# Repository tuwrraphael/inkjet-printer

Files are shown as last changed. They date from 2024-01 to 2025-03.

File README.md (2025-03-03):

# Inkjet Printer

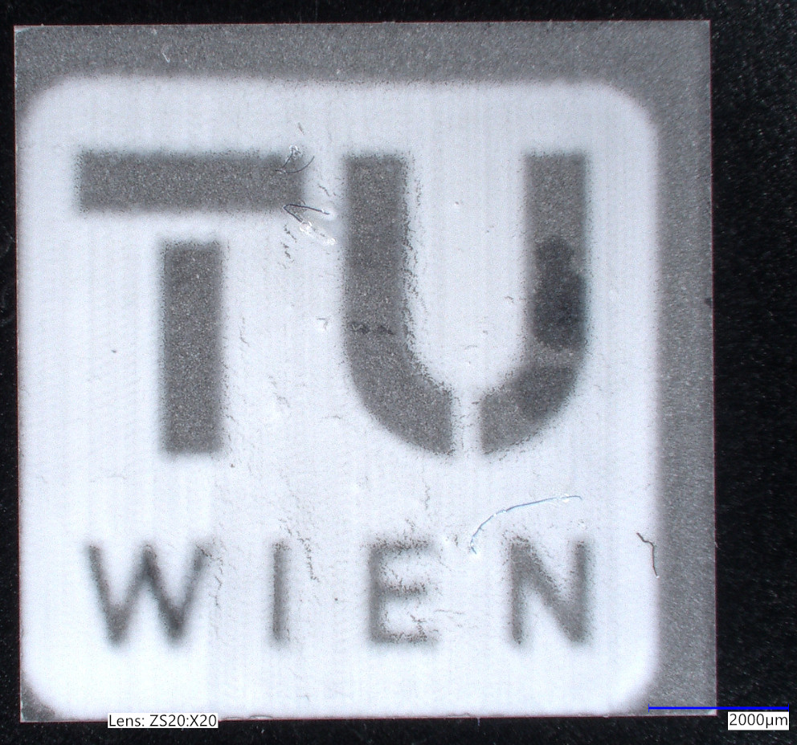
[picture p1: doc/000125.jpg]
A microscope image of a printed TU Wien logo on a 10mm x 10mm substrate.


This repository contains the code, PCB, and CAD of the custom-designed inkjet printer for printing ceramic thin films, which was created as part of the master thesis [Development of an Inkjet Printer for Electrolyte Layers of Oxygen Ion Batteries](https://doi.org/10.34726/hss.2024.116604).
<br clear="right"/>

---

See a preview of the control software: [https://tuwrraphael.github.io/inkjet-printer/](https://tuwrraphael.github.io/inkjet-printer/).

<p align="center">
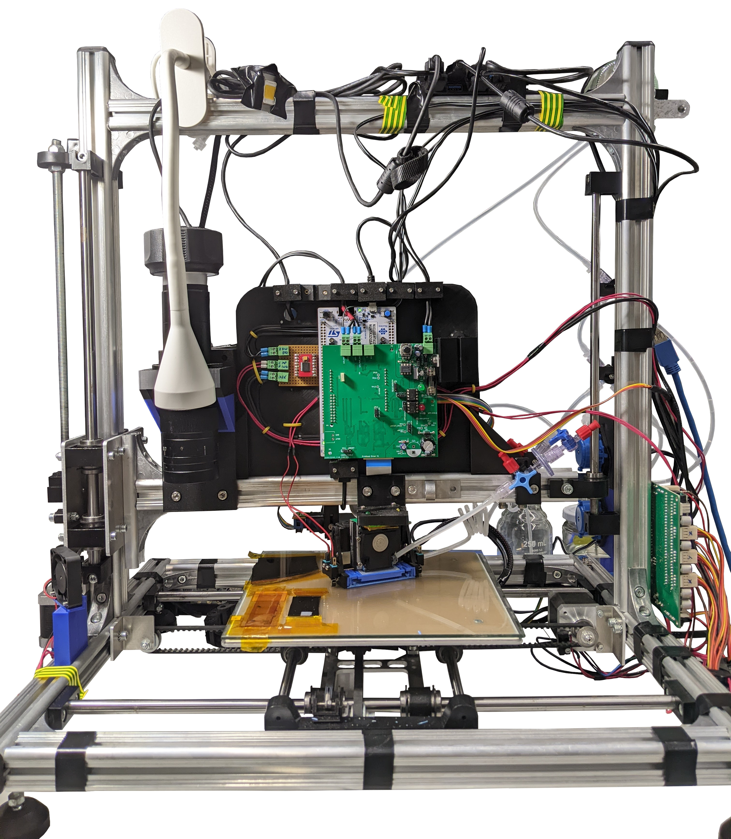
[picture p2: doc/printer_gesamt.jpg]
An overview image of the implemented inkjet printer.
 
 <br>
 An overview image of the implemented inkjet printer.
</p>

Details about the printer, challenges and design decisions, its application and evaluation can be found in the [thesis](https://repositum.tuwien.at/bitstream/20.500.12708/208972/1/Hauk%20Raphael%20-%202024%20-%20Development%20of%20an%20Inkjet%20Printer%20for%20Electrolyte%20Layers%20o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).

Repository structure:
* [inkjet-printer-app](inkjet-printer-app): A web app that controls the printer, is used for planning print jobs, print monitoring & evaluation, calibration and maintenance. Runs in a browser using WebUSB and WebSerial for communicating with the hardware. A deployed version to test an be found [here](https://tuwrraphael.github.io/inkjet-printer/).
* [inkjet-printer-zephyr](inkjet-printer-zephyr): The Zephyr based firmware of the printhead drive electronics.
* [pcbs/Xaar128-Driver](pcbs/Xaar128-Driver): The main PBC design of the printhead drive electronics.
* [cad](cad): Various CAD files of attachments added to the printer.

## Cite this work
The main purpose of publishing this repository is to provide insights into the development of a custom inkjet printer. If you got inspired or found parts of this project useful, please cite the thesis.
~~~
@mastersthesis{HaukRaphael2024DoaI,
  title = {Development of an Inkjet Printer for Electrolyte Layers of Oxygen Ion Batteries},
  author = {Hauk, Raphael},
  year    = 2024,
  school  = {TU Wien},
  address = {Vienna, Austria},
  type    = {{Master's thesis}},
  note     = {Available at: \url{https://doi.org/10.34726/hss.2024.116604}}
}
~~~

## Acknowledgements
This research was funded in part by the Austrian Science Fund (FWF) [10.55776/COE5](https://doi.org/10.55776/COE5).

## Licensing
The firmware builds on Zephyr Project, which is licensed under the Apache License 2.0.
Tools and libraries used in the control software are listed in the app [here](https://tuwrraphael.github.io/inkjet-printer/info).

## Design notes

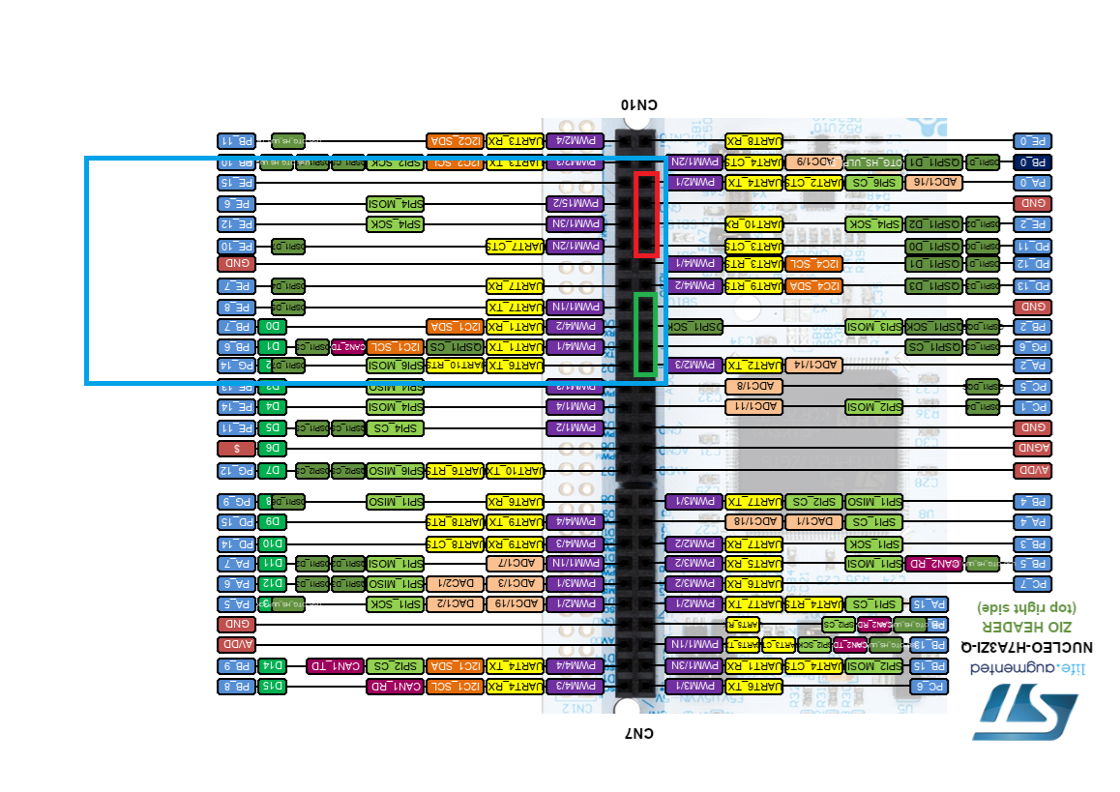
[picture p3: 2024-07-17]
pcbs/pump/pump-pins.png

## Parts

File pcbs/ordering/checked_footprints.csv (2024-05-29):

Value | Footprint | RSBestNr
10u >72V E | Capacitor_THT:CP_Radial_D5.0mm_P2.00mm | 228-7079
220u >72V E | Capacitor_THT:CP_Radial_D13.0mm_P5.00mm | 711-1734
1u >72V Cer | Capacitor_SMD:C_0805_2012Metric_Pad1.18x1.45mm_HandSolder | 788-3054
2.2u >72V E | Capacitor_THT:CP_Radial_D5.0mm_P2.00mm | 365-4442
100n >16V Film | Capacitor_THT:C_Rect_L7.0mm_W3.5mm_P5.00mm | 463-1765
BZX84C10LT1G 10V | Package_TO_SOT_SMD:SOT-23 | 625-5256
3.3V | Diode_SMD:D_SOD-123F | 792-0936
BZX84C27LT1G 27V | Package_TO_SOT_SMD:SOT-23 | 687-8187
Heatsink | Xaar-Driver:SK68-375-SA | 189-8498
Screw_Terminal_01x02 | RS_PRO:897-1051 | 897-1051 + 897-0998
SolderJumper_2_Bridged | Resistor_SMD:R_0603_1608Metric_Pad0.98x0.95mm_HandSolder | 820-6736
DMN2075U | Package_TO_SOT_SMD:SOT-23 | 751-4143
DMG2305UX | Package_TO_SOT_SMD:SOT-23 | 827-0452
1.2k | Resistor_SMD:R_0603_1608Metric_Pad0.98x0.95mm_HandSolder | 198-5480
31.6k | Resistor_SMD:R_0603_1608Metric_Pad0.98x0.95mm_HandSolder | 708-8877
5.1k | Resistor_SMD:R_0603_1608Metric_Pad0.98x0.95mm_HandSolder | 198-5552
68k | Resistor_SMD:R_0603_1608Metric_Pad0.98x0.95mm_HandSolder | 566-367
1.6k | Resistor_SMD:R_0603_1608Metric_Pad0.98x0.95mm_HandSolder | 242-4070
1k | Resistor_SMD:R_0603_1608Metric_Pad0.98x0.95mm_HandSolder | 678-9875
5.1k >300mW | Resistor_SMD:R_0805_2012Metric_Pad1.20x1.40mm_HandSolder | 721-7804
2k > 700mW | Resistor_SMD:R_2010_5025Metric_Pad1.40x2.65mm_HandSolder | 186-6957
100k | Resistor_SMD:R_0603_1608Metric_Pad0.98x0.95mm_HandSolder | 678-9673
12k > 200mW | Resistor_SMD:R_1206_3216Metric_Pad1.30x1.75mm_HandSolder | 812-1795
200 | Resistor_THT:R_Axial_DIN0207_L6.3mm_D2.5mm_P7.62mm_Horizontal | 148-332
4.7k | Resistor_SMD:R_0603_1608Metric_Pad0.98x0.95mm_HandSolder | 901-3581
2.2k > 600mW | Resistor_SMD:R_2512_6332Metric_Pad1.40x3.35mm_HandSolder | 755-1287
680 | Resistor_SMD:R_0603_1608Metric_Pad0.98x0.95mm_HandSolder | 679-0627
6N135 | Package_DIP:DIP-8_W7.62mm | 691-2316
74HC173 | Package_SO:SO-16_3.9x9.9mm_P1.27mm | 483-6443
NUCLEO-H743ZI2 | Xaar-Driver:NUCLEO-H743 | 193-9787
74AHCT125 | Package_SO:SOIC-14_3.9x8.7mm_P1.27mm | 798-8941
LM317_TO-220 | Package_TO_SOT_THT:TO-220-3_Vertical | 661-6121
LTV-356T | Package_SO:SO-4_4.4x3.6mm_P2.54mm | 691-2079
5.1k | Resistor_SMD:R_0805_2012Metric_Pad1.20x1.40mm_HandSolder | 721-7804
Conn_02x15_Odd_Even | CONN_9-176140-0:CONN_9-176140-0_TYC | 7025214
0 | Resistor_SMD:R_0603_1608Metric_Pad0.98x0.95mm_HandSolder | 820-6736
470 | Resistor_SMD:R_0603_1608Metric_Pad0.98x0.95mm_HandSolder | 566-547
NUCLEO-H743ZI2 | Xaar-Driver:NUCLEO-H743 | 198-8645
10u > 16V Tantal | Capacitor_Tantalum_SMD:CP_EIA-3528-21_Kemet-B_Pad1.50x2.35mm_HandSolder | 136-0203
12k | Resistor_SMD:R_1206_3216Metric_Pad1.30x1.75mm_HandSolder | 812-1795
MCP4725xxx-xCH | Package_TO_SOT_SMD:SOT-23-6_Handsoldering | 669-6290
L7824 | Package_TO_SOT_THT:TO-220-3_Vertical | 298-8564
MC78L05_SOT89 | Xaar-Driver:SOT-89-3 | 714-0679
MCP3021 | Package_TO_SOT_SMD:SOT-23-5_HandSoldering | 738-6011
ISO1541 | Package_SO:SOIC-8_3.9x4.9mm_P1.27mm | 825-3075

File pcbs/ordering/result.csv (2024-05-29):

# | Reference | Qty | Value | Footprint | DNP | Supplier | RSBestNr | Extension | done
1 | C1, C2, C3, C4, C5, C6, C28, C30, C33 | 9 | 100n >16V Cer | Capacitor_SMD:C_0603_1608Metric_Pad1.08x0.95mm_HandSolder | DNP | Elektroplatz |  |  | true
2 | C7, C8, C9, C10, C29, C31 | 6 | 100n >16V Cer | Capacitor_SMD:C_0603_1608Metric_Pad1.08x0.95mm_HandSolder |  | Elektroplatz |  |  | true
3 | C11, C16 | 2 | 1u >72V Cer | Capacitor_SMD:C_0805_2012Metric_Pad1.18x1.45mm_HandSolder | DNP | RS | 788-3054 |  | true
4 | C12, C18 | 2 | 10u >72V E | Capacitor_THT:CP_Radial_D5.0mm_P2.00mm |  | RS | 228-7079 |  | true
5 | C13 | 1 | 220u >72V E | Capacitor_THT:CP_Radial_D13.0mm_P5.00mm |  | RS | 711-1734 |  | true
6 | C14 | 1 | 220u >72V E | Capacitor_THT:CP_Radial_D13.0mm_P5.00mm | DNP | RS | 711-1734 |  | true
7 | C15 | 1 | 1u >72V Cer | Capacitor_SMD:C_0805_2012Metric_Pad1.18x1.45mm_HandSolder |  | RS | 788-3054 |  | true
8 | C17, C19 | 2 | 2.2u >72V E | Capacitor_THT:CP_Radial_D5.0mm_P2.00mm |  | RS | 365-4442 |  | true
9 | C20, C25 | 2 | 10u > 16V Tantal | Capacitor_Tantalum_SMD:CP_EIA-3528-21_Kemet-B_Pad1.50x2.35mm_HandSolder | DNP | RS | 136-0203 | Regulator | true
10 | C21, C22, C23, C24, C26 | 5 | 100n >16V Cer | Capacitor_SMD:C_0603_1608Metric_Pad1.08x0.95mm_HandSolder | DNP | Elektroplatz |  | Regulator | true
11 | C27 | 1 | 100n >16V Film | Capacitor_THT:C_Rect_L7.0mm_W3.5mm_P5.00mm |  | RS | 463-1765 |  | true
12 | D1 | 1 | BZX84C10LT1G 10V | Package_TO_SOT_SMD:SOT-23 |  | RS | 625-5256 |  | true
13 | D3 | 1 | LED green Vf=1.8V | Custom_LED_THT:LED_D5.0mm |  | Elektroplatz |  |  | true
14 | D4 | 1 | LED red Vf=1.6V | Custom_LED_THT:LED_D5.0mm |  | Elektroplatz |  |  | true
15 | D5 | 1 | 3.3V | Diode_SMD:D_SOD-123F |  | RS | 792-0936 |  | true
16 | D6 | 1 | BZX84C27LT1G 27V | Package_TO_SOT_SMD:SOT-23 |  | RS | 687-8187 |  | true
17 | D7, D10 | 2 | 1N4007 | Diode_THT:D_DO-41_SOD81_P10.16mm_Horizontal |  | Elektroplatz |  |  | true
18 | D8 | 1 | 1N4007 | Diode_THT:D_DO-41_SOD81_P12.70mm_Horizontal |  | Elektroplatz |  |  | true
19 | D9 | 1 | 5.1V | Diode_THT:D_DO-35_SOD27_P7.62mm_Horizontal |  | Elektroplatz |  |  | true
20 | F1 | 1 | 630mA/F | FUSE_646_1_LTF:FUSE_646_1_LTF |  | Printerbox |  |  | true
21 | H1, H2, H3, H4 | 4 | MountingHole | MountingHole:MountingHole_2.7mm_M2.5_DIN965 |  | None |  |  | true
22 | HS1 | 1 | Heatsink | Xaar-Driver:SK68-375-SA |  | RS | 189-8498 |  | true
23 | J1, J2, J3, J4, J7 | 5 | Screw_Terminal_01x02 | RS_PRO:897-1051 |  | RS | 897-1051 + 897-0998 |  | true
24 | J5 | 1 | Conn_01x21 | Molex_200528:Molex_200528-0210_1x21-1MP_P1.00mm_Horizontal |  | Printerbox |  |  | true
25 | J6 | 1 | Conn_02x08_Odd_Even | Connector_IDC:IDC-Header_2x08_P2.54mm_Vertical | DNP | RS | 771-8357 |  | true
26 | JP1, JP2, JP4, JP5, JP6, JP7, JP14 | 7 | Jumper_3_Bridged12 | Connector_PinHeader_2.54mm:PinHeader_1x03_P2.54mm_Vertical |  | Elektroplatz |  |  | true
27 | JP3, JP8, JP9, JP13, JP15 | 5 | SolderJumper_2_Bridged | Resistor_SMD:R_0603_1608Metric_Pad0.98x0.95mm_HandSolder |  | RS | 820-6736 |  | true
28 | JP10, JP11, JP12, JP16, JP17, JP18, JP19, JP20 | 8 | SolderJumper_2_Open | Resistor_SMD:R_0603_1608Metric_Pad0.98x0.95mm_HandSolder |  | None |  |  | true
29 | Q1, Q2, Q3, Q4, Q5, Q6, Q9, Q10 | 8 | DMN2075U | Package_TO_SOT_SMD:SOT-23 |  | RS | 751-4143 |  | true
30 | Q7, Q8 | 2 | DMG2305UX | Package_TO_SOT_SMD:SOT-23 |  | RS | 827-0452 |  | true
31 | Q11 | 1 | DMG2305UX | Package_TO_SOT_SMD:SOT-23 | DNP | RS | 827-0452 |  | true
32 | R1 | 1 | 1.2k | Resistor_SMD:R_0603_1608Metric_Pad0.98x0.95mm_HandSolder |  | RS | 198-5480 |  | true
33 | R2 | 1 | 31.6k | Resistor_SMD:R_0603_1608Metric_Pad0.98x0.95mm_HandSolder |  | RS | 708-8877 |  | true
34 | R3, R28 | 2 | 5.1k | Resistor_SMD:R_0805_2012Metric_Pad1.20x1.40mm_HandSolder |  | RS | 721-7804 |  | true
35 | R4 | 1 | 68k | Resistor_SMD:R_0603_1608Metric_Pad0.98x0.95mm_HandSolder |  | RS | 566-367 |  | true
36 | R5, R6 | 2 | 1.6k | Resistor_SMD:R_0603_1608Metric_Pad0.98x0.95mm_HandSolder |  | RS | 242-4070 |  | true
37 | R7, R8, R12, R22, R25, R29, R55, R58 | 8 | 1k | Resistor_SMD:R_0603_1608Metric_Pad0.98x0.95mm_HandSolder |  | RS | 678-9875 |  | true
38 | R9 | 1 | 5.1k >300mW | Resistor_SMD:R_0805_2012Metric_Pad1.20x1.40mm_HandSolder |  | RS | 721-7804 |  | true
39 | R10 | 1 | 2k > 700mW | Resistor_SMD:R_2010_5025Metric_Pad1.40x2.65mm_HandSolder |  | RS | 186-6957 |  | true
40 | R11, R20, R23, R46, R56 | 5 | 100k | Resistor_SMD:R_0603_1608Metric_Pad0.98x0.95mm_HandSolder |  | RS | 678-9673 |  | true
41 | R13 | 1 | 20k | Resistor_SMD:R_0603_1608Metric_Pad0.98x0.95mm_HandSolder |  | Elektroplatz |  |  | true
42 | R14, R15, R16, R17, R21, R26, R43, R44, R45, R50, R51, R52, R54 | 13 | 10k | Resistor_SMD:R_0603_1608Metric_Pad0.98x0.95mm_HandSolder |  | Elektroplatz |  |  | true
43 | R18, R33, R47, R48, R49, R53 | 6 | 10k | Resistor_SMD:R_0603_1608Metric_Pad0.98x0.95mm_HandSolder | DNP | Elektroplatz |  |  | true
44 | R19, R24 | 2 | 100k | Resistor_SMD:R_0603_1608Metric_Pad0.98x0.95mm_HandSolder | DNP | RS | 678-9673 |  | true
45 | R27 | 1 | 12k > 200mW | Resistor_SMD:R_1206_3216Metric_Pad1.30x1.75mm_HandSolder |  | RS | 812-1795 |  | true
46 | R30 | 1 | 200 | Resistor_THT:R_Axial_DIN0207_L6.3mm_D2.5mm_P7.62mm_Horizontal |  | RS | 148-332 |  | true
47 | R31 | 1 | 4.7k | Resistor_SMD:R_0603_1608Metric_Pad0.98x0.95mm_HandSolder |  | RS | 901-3581 |  | true
48 | R32 | 1 | 2.2k > 600mW | Resistor_SMD:R_2512_6332Metric_Pad1.40x3.35mm_HandSolder |  | RS | 755-1287 |  | true
49 | R34, R35, R36 | 3 | 10k | Resistor_SMD:R_0603_1608Metric_Pad0.98x0.95mm_HandSolder | DNP | Elektroplatz |  | Regulator | true
50 | R37, R41 | 2 | 100k | Resistor_SMD:R_0603_1608Metric_Pad0.98x0.95mm_HandSolder | DNP | RS | 678-9673 | Regulator | true
51 | R38 | 1 | 2.2k | Resistor_SMD:R_0603_1608Metric_Pad0.98x0.95mm_HandSolder | DNP | Elektroplatz |  | Regulator | true
52 | R39, R42 | 2 | 12k | Resistor_SMD:R_1206_3216Metric_Pad1.30x1.75mm_HandSolder | DNP | RS | 812-1795 | Regulator | true
53 | R40 | 1 | 3k | Resistor_THT:R_Axial_DIN0207_L6.3mm_D2.5mm_P7.62mm_Horizontal | DNP | Elektroplatz |  | Regulator | true
54 | R57 | 1 | 2.2k | Resistor_SMD:R_0603_1608Metric_Pad0.98x0.95mm_HandSolder |  | Elektroplatz |  |  | true
55 | R59 | 1 | 680 | Resistor_SMD:R_0603_1608Metric_Pad0.98x0.95mm_HandSolder |  | RS | 679-0627 |  | true
56 | RV1 | 1 | 10k RC103B | Potentiometer_THT:Potentiometer_Alps_RK09L_Single_Vertical |  | Elektroplatz |  |  | true
57 | TP1, TP2, TP3, TP4, TP5, TP6, TP7, TP8, TP9, TP10, TP11, TP12, TP13, TP14, TP15 | 15 | TestPoint | Xaar-Driver:TestPoint_Pad_D1.5mm |  | None |  |  | true
58 | U1, U2 | 2 | 6N135 | Package_DIP:DIP-8_W7.62mm |  | RS | 691-2316 |  | true
59 | U3, U21 | 2 | 74HC173 | Package_SO:SO-16_3.9x9.9mm_P1.27mm |  | RS | 483-6443 |  | true
60 | U4 | 1 | NUCLEO-H743ZI2 | Xaar-Driver:NUCLEO-H743 |  | RS | 198-8645 |  | true
61 | U5, U6, U7, U12 | 4 | TXB0104D | Package_SO:SOIC-14_3.9x8.7mm_P1.27mm | DNP | RS | 709-2778 |  | true
62 | U8, U9, U10, U20 | 4 | 74AHCT125 | Package_SO:SOIC-14_3.9x8.7mm_P1.27mm |  | RS | 798-8941 |  | true
63 | U11 | 1 | LM317_TO-220 | Package_TO_SOT_THT:TO-220-3_Vertical |  | RS | 661-6121 |  | true
64 | U13 | 1 | MCP4725xxx-xCH | Package_TO_SOT_SMD:SOT-23-6_Handsoldering | DNP | RS | 669-6290 | Regulator | true
65 | U14 | 1 | ISO1541 | Package_SO:SOIC-8_3.9x4.9mm_P1.27mm | DNP | RS | 825-3075 | Regulator | true
66 | U15 | 1 | L7824 | Package_TO_SOT_THT:TO-220-3_Vertical | DNP | RS | 298-8564 | Regulator | true
67 | U16 | 1 | MC78L05_SOT89 | Xaar-Driver:SOT-89-3 | DNP | RS | 714-0679 | Regulator | true
68 | U17 | 1 | TLC272 | Package_DIP:DIP-8_W7.62mm | DNP | Elektroplatz |  | Regulator | true
69 | U18 | 1 | MCP3021 | Package_TO_SOT_SMD:SOT-23-5_HandSoldering | DNP | RS | 738-6011 | Regulator | true
70 | U19 | 1 | LTV-356T | Package_SO:SO-4_4.4x3.6mm_P2.54mm |  | RS | 691-2079 |  | true
71 | U22 | 1 | LIS2DH | Package_LGA:LGA-14_2x2mm_P0.35mm_LayoutBorder3x4y | DNP | None |  |  | true
1 | D1 | 1 | LED yellow Vf=1.6V | Custom_LED_THT:LED_D3.0mm |  | Elektroplatz |  |  | true
2 | D2 | 1 | LED green Vf=1.8V | Custom_LED_THT:LED_D3.0mm |  | Elektroplatz |  |  | true
3 | H1, H2 | 2 | MountingHole | MountingHole:MountingHole_2.7mm_M2.5_DIN965 |  | None |  |  | true
4 | J1 | 1 | Conn_01x21 | Molex_200528:Molex_200528-0210_1x21-1MP_P1.00mm_Horizontal |  | Printerbox |  |  | true
5 | J2 | 1 | Conn_02x15_Odd_Even | CONN_9-176140-0:CONN_9-176140-0_TYC |  | Printerbox | 7025214 |  | true
6 | J3 | 1 | Conn_01x12 | Molex_200528:Molex_52207-1260_1x12-1MP_P1.00mm_Horizontal | DNP | RS | 670-6754 |  | true
7 | Q1 | 1 | DMN2075U | Package_TO_SOT_SMD:SOT-23 |  | RS | 751-4143 |  | true
8 | R1 | 1 | 0 | Resistor_SMD:R_0603_1608Metric_Pad0.98x0.95mm_HandSolder |  | RS | 820-6736 |  | true
9 | R2 | 1 | 10K | Resistor_SMD:R_0603_1608Metric_Pad0.98x0.95mm_HandSolder | DNP | Elekroplatz |  |  | true
10 | R3 | 1 | 1k | Resistor_SMD:R_0603_1608Metric_Pad0.98x0.95mm_HandSolder |  | RS | 678-9875 |  | true
11 | R4 | 1 | 470 | Resistor_SMD:R_0603_1608Metric_Pad0.98x0.95mm_HandSolder |  | RS | 566-547 |  | true
12 | R6 | 1 | 5.1k >300mW | Resistor_SMD:R_0805_2012Metric_Pad1.20x1.40mm_HandSolder |  | RS | 721-7804 |  | true

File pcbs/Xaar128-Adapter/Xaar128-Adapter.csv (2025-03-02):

# | Reference | Qty | Value | Footprint | DNP | Supplier | RSBestNr | Extension
1 | D1 | 1 | LED yellow Vf=1.6V | Custom_LED_THT:LED_D3.0mm |  | Elektroplatz
2 | D2 | 1 | LED green Vf=1.8V | Custom_LED_THT:LED_D3.0mm |  | Elektroplatz
3 | H1, H2 | 2 | MountingHole | MountingHole:MountingHole_2.7mm_M2.5_DIN965 |  | None
4 | J1 | 1 | Conn_01x21 | Molex_200528:Molex_200528-0210_1x21-1MP_P1.00mm_Horizontal |  | Printerbox
5 | J2 | 1 | Conn_02x15_Odd_Even | CONN_9-176140-0:CONN_9-176140-0_TYC |  | Printerbox | 7025214
6 | J3 | 1 | Conn_01x12 | Molex_200528:Molex_52207-1260_1x12-1MP_P1.00mm_Horizontal | DNP | RS | 670-6754
7 | Q1 | 1 | DMN2075U | Package_TO_SOT_SMD:SOT-23 |  | RS | 751-4143
8 | R1 | 1 | 0 | Resistor_SMD:R_0603_1608Metric_Pad0.98x0.95mm_HandSolder |  | RS | 820-6736
9 | R2 | 1 | 10K | Resistor_SMD:R_0603_1608Metric_Pad0.98x0.95mm_HandSolder | DNP | Elekroplatz
10 | R3 | 1 | 1k | Resistor_SMD:R_0603_1608Metric_Pad0.98x0.95mm_HandSolder |  | RS | 678-9875
11 | R4 | 1 | 470 | Resistor_SMD:R_0603_1608Metric_Pad0.98x0.95mm_HandSolder |  | RS | 566-547
12 | R6 | 1 | 5.1k >300mW | Resistor_SMD:R_0805_2012Metric_Pad1.20x1.40mm_HandSolder |  | RS | 721-7804

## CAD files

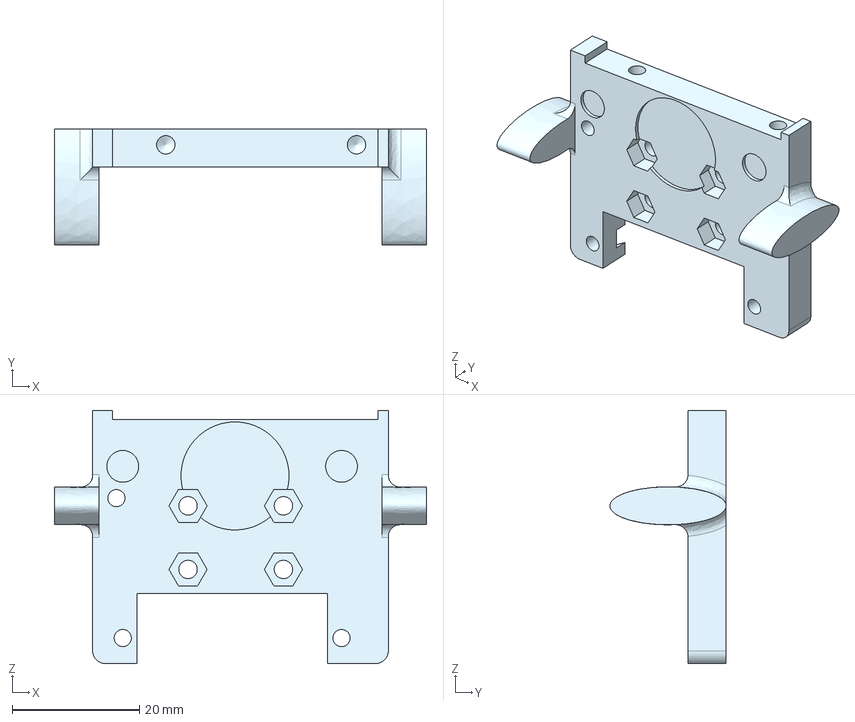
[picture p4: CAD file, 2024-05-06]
cad/Holder - Printheadfixture.step
58.5 x 18.3 x 39.8 mm

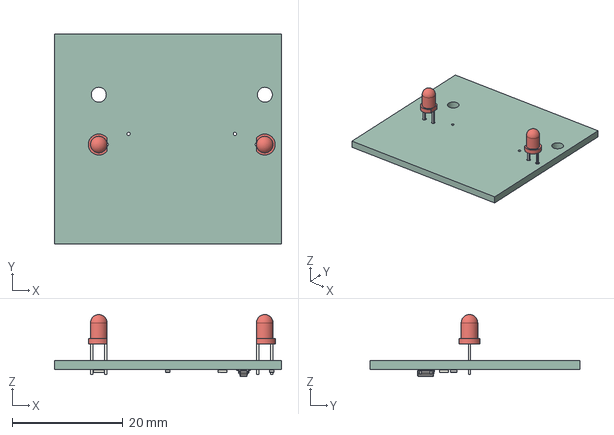
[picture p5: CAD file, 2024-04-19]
cad/Xaar128-Adapter.step
41.0 x 38.0 x 11.2 mm
Xaar128-Adapter PCB

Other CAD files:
cad/Beltspanner.ipt
cad/CameraHolderV2.ipt
cad/Capping_Assembly2.iam
cad/Capping_Insert.ipt
cad/Capping_RotatingArm.ipt
cad/Capping_RotatingCover.ipt
cad/Capping_RotationAnchor.ipt
cad/Capping_RotationGuide.ipt
cad/Capping_RotationGuide_MIR.ipt
cad/Capping_RubberInsert.ipt
cad/Clip.ipt
cad/Dreiwegehahn_Halter.ipt
cad/Dreiwegehahn_Montage45.ipt
cad/Encoder1.iam
cad/Encoder_Mount1.iam
cad/Encoder_Mount1_Slider.ipt
cad/Encoder_Mount2.iam
cad/Encoder_Mount2.ipt
cad/Encoder_Mount3.iam
cad/Encoder_Mount3_Base.ipt
cad/Encoder_Mount3_Washer.ipt
cad/Encoder_Mount3_Wheel.ipt
cad/Enoder_Mount1.ipt
cad/Microscope_Mount.ipt
cad/PCB_Mount_Triangle.ipt
cad/PCB_Plate.ipt
cad/Pressuresensor_Holder.ipt
cad/Pressurevessel_Mount.ipt
cad/Printer_Mount.ipt
cad/Pump_Mount.ipt
cad/Sensor_Montage.ipt
cad/TPiece.ipt
cad/Xaar128.ipt

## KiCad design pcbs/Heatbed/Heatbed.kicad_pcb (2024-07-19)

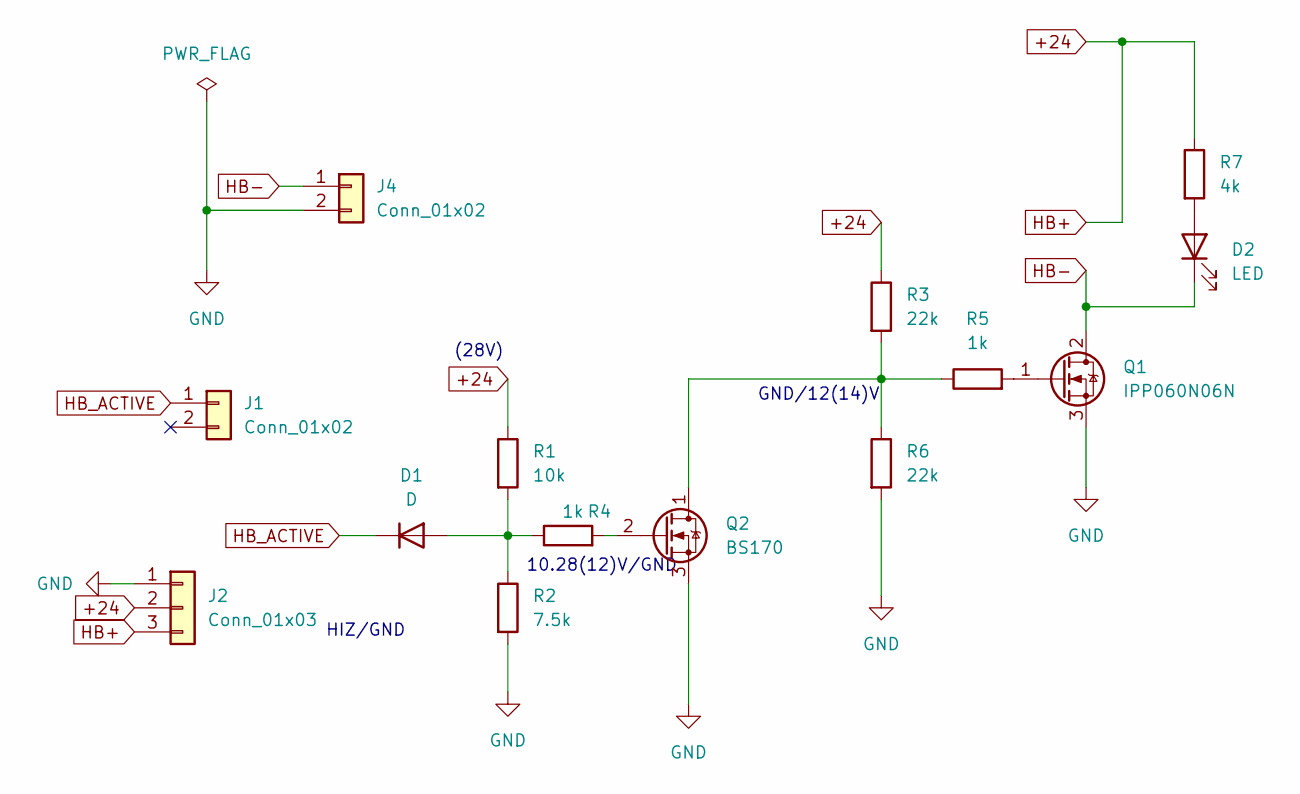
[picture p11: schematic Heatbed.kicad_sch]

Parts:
D1: D; D_A-405_P7.62mm_Horizontal
D2: LED; LED_D3.0mm
J1: Conn_01x02; PinHeader_1x02_P2.54mm_Vertical
J2: Conn_01x03; TerminalBlock_bornier-3_P5.08mm
J4: Conn_01x02; TerminalBlock_bornier-2_P5.08mm
Q1: IPP060N06N; TO-220-3_Vertical
Q2: BS170; TO-92_Inline_Wide
R1: 10k; R_Axial_DIN0204_L3.6mm_D1.6mm_P5.08mm_Horizontal
R2: 7.5k; R_Axial_DIN0204_L3.6mm_D1.6mm_P5.08mm_Horizontal
R3, R6: 22k; R_Axial_DIN0204_L3.6mm_D1.6mm_P5.08mm_Horizontal
R4, R5: 1k; R_Axial_DIN0204_L3.6mm_D1.6mm_P5.08mm_Horizontal
R7: 4k; R_Axial_DIN0204_L3.6mm_D1.6mm_P5.08mm_Horizontal

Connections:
+24: J2.2, J2.3, R1.1, R3.1, R7.1
GND: J2.1, J4.2, Q1.3 (S), Q2.3 (S), R2.2, R6.2
HB-: D2.1 (K), J4.1, Q1.2 (D)
HB_ACTIVE: D1.1 (K), J1.1
unnamed: D1.2 (A), R1.2, R2.1, R4.1
unnamed: D2.2 (A), R7.2
unnamed: Q1.1 (G), R5.2
unnamed: Q2.1 (D), R3.2, R5.1, R6.1
unnamed: Q2.2 (G), R4.2

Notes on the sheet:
HIZ/GND
(28V)
10.28(12)V/GND
GND/12(14)V

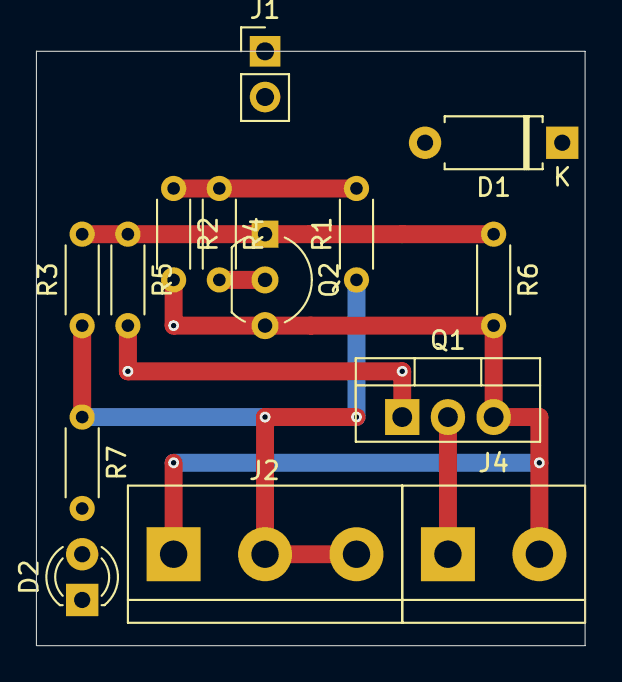
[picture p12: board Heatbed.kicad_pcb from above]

Board: 2 copper layers, 30.5 x 33.0 mm, 14 parts (0 on the bottom side), 9 nets.

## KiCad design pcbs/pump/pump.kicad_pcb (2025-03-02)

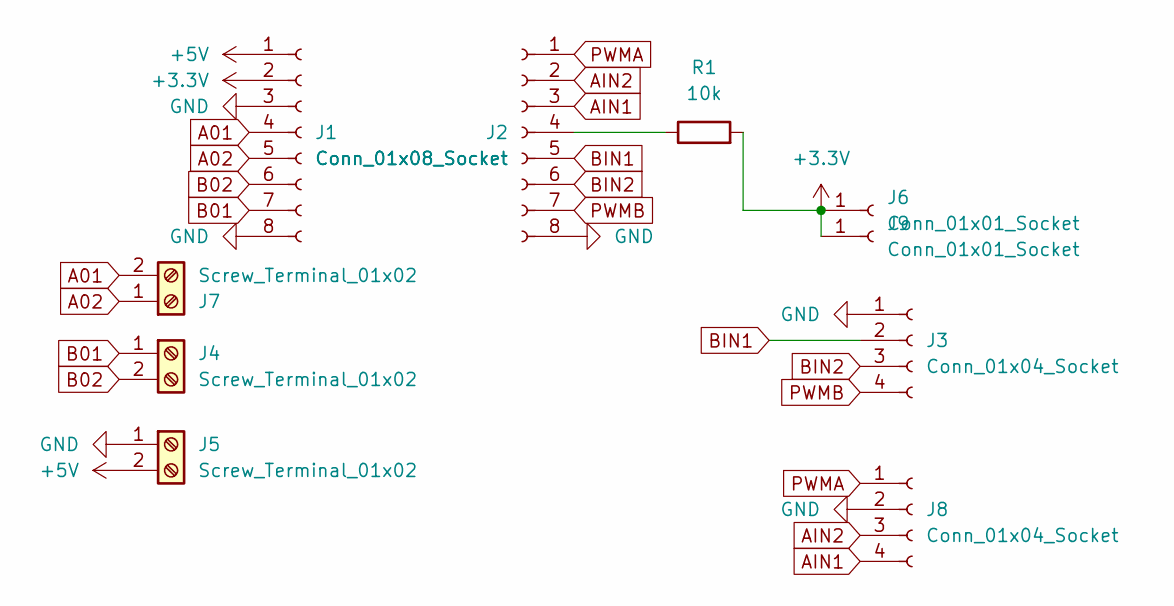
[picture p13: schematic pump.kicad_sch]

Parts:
J1, J2: Conn_01x08_Socket; PinSocket_1x08_P2.54mm_Vertical
J3, J8: Conn_01x04_Socket; PinSocket_1x04_P2.54mm_Vertical
J4, J5, J7: Screw_Terminal_01x02; Steckbarer_Klemmenblock_1x02_5.08mm_horizontal
J6, J9: Conn_01x01_Socket; PinSocket_1x01_P2.54mm_Vertical
R1: 10k; R_Axial_DIN0207_L6.3mm_D2.5mm_P7.62mm_Horizontal

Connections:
+3.3V: J1.2, J6.1, J9.1, R1.2
+5V: J1.1, J5.2
A01: J1.4, J7.2
A02: J1.5, J7.1
AIN1: J2.3, J8.4
AIN2: J2.2, J8.3
B01: J1.7, J4.1
B02: J1.6, J4.2
BIN1: J2.5, J3.2
BIN2: J2.6, J3.3
GND: J1.3, J1.8, J2.8, J3.1, J5.1, J8.2
unnamed: J2.4, R1.1
PWMA: J2.1, J8.1
PWMB: J2.7, J3.4

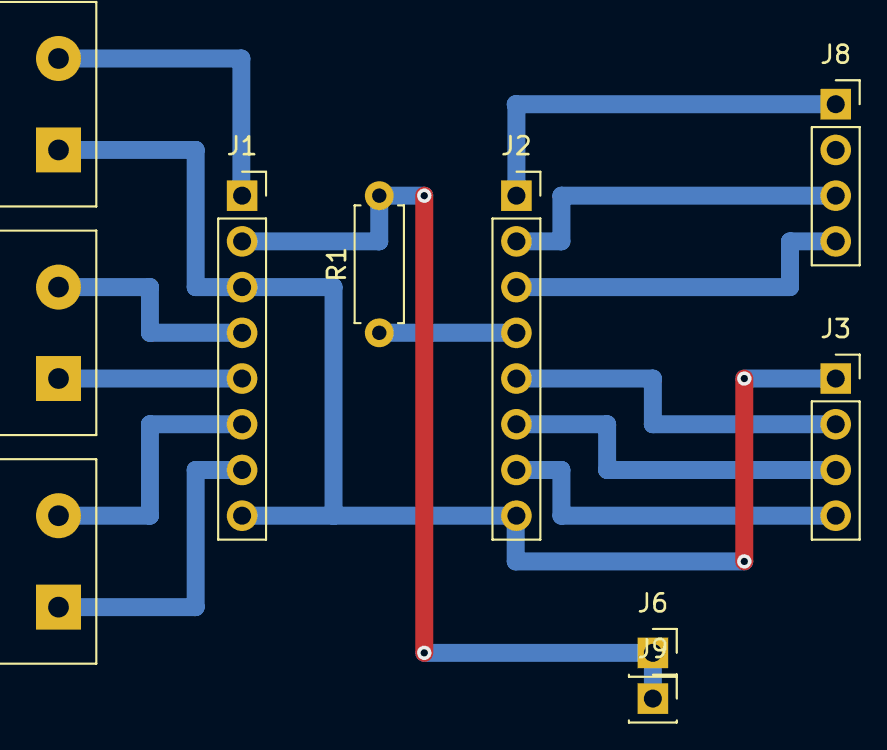
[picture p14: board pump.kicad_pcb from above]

Board: 2 copper layers, 10 parts (0 on the bottom side), 14 nets.

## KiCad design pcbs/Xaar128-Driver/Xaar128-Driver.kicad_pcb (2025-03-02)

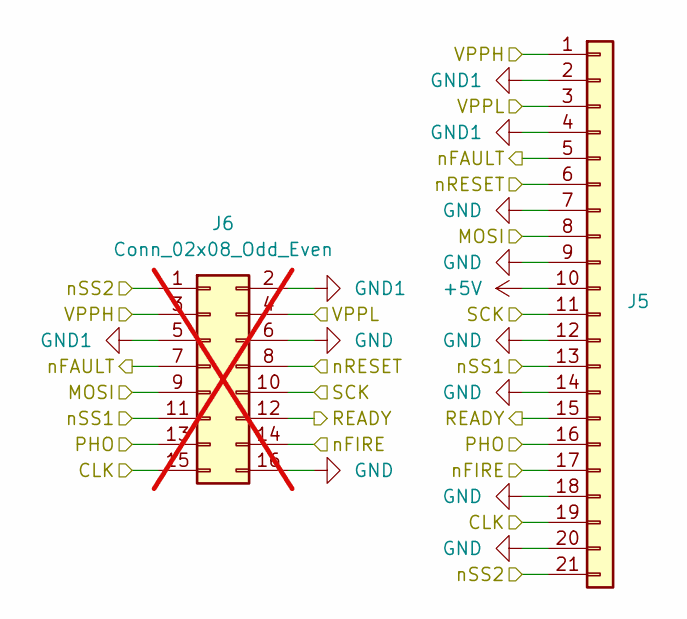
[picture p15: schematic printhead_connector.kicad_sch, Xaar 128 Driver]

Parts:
J5: Conn_01x21; Molex_200528-0210_1x21-1MP_P1.00mm_Horizontal
J6: Conn_02x08_Odd_Even; IDC-Header_2x08_P2.54mm_Vertical; not fitted

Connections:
+5V: J5.10; also elsewhere on the board
/HV Supply/VPPH: J5.1, J6.3; also elsewhere on the board
/HV Supply/VPPL: J5.3, J6.4; also elsewhere on the board
/IO/nFIRE: J5.17, J6.14; also elsewhere on the board
/Level Shift/CLK_OUT: J5.19, J6.15; also elsewhere on the board
/Level Shift/MOSI_OUT: J5.8, J6.9; also elsewhere on the board
/Level Shift/PHO_OUT: J5.16, J6.13; also elsewhere on the board
/Level Shift/READY_IN: J5.15, J6.12; also elsewhere on the board
/Level Shift/SCK_OUT: J5.11, J6.10; also elsewhere on the board
/Level Shift/nFAULT_IN: J5.5, J6.7; also elsewhere on the board
/Level Shift/nRESET_IN: J5.6, J6.8; also elsewhere on the board
/Level Shift/nSS1_OUT: J5.13, J6.11; also elsewhere on the board
/Level Shift/nSS2_OUT: J5.21, J6.1; also elsewhere on the board

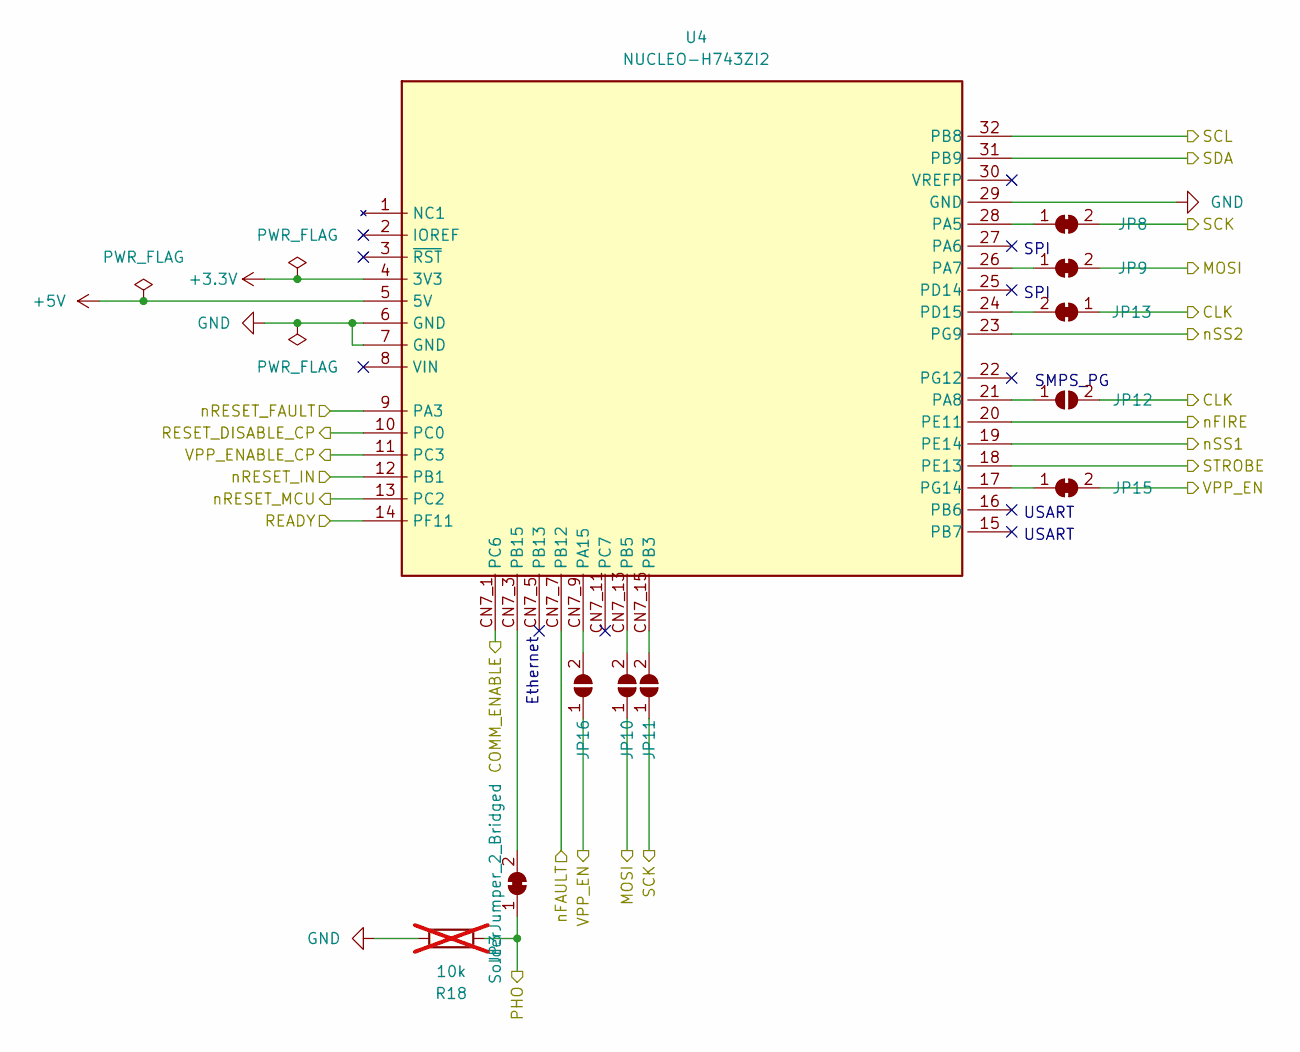
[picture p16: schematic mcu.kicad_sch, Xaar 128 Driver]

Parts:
JP3, JP8, JP9, JP13, JP15: SolderJumper_2_Bridged; R_0603_1608Metric_Pad0.98x0.95mm_HandSolder
JP10, JP11, JP12, JP16: SolderJumper_2_Open; R_0603_1608Metric_Pad0.98x0.95mm_HandSolder
R18: 10k; R_0603_1608Metric_Pad0.98x0.95mm_HandSolder; not fitted
U4: NUCLEO-H743ZI2; NUCLEO-H743

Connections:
+5V: U4.5 (5V); also elsewhere on the board
/ACC/SCL: U4.32 (PB8); also elsewhere on the board
/ACC/SDA: U4.31 (PB9); also elsewhere on the board
/HV Supply/VPP_EN: JP15.2 (B), JP16.1 (A); also elsewhere on the board
/Level Shift/CLK_IN: JP12.2 (B), JP13.1 (A); also elsewhere on the board
/Level Shift/COMM_ENABLE: U4.CN7_1 (PC6); also elsewhere on the board
/Level Shift/MOSI_IN: JP9.2 (B), JP10.1 (A); also elsewhere on the board
/Level Shift/PHO_IN: JP3.1 (A), R18.2; also elsewhere on the board
/Level Shift/READY_OUT: U4.14 (PF11); also elsewhere on the board
/Level Shift/RESET_DISABLE_CP_IN: U4.10 (PC0); also elsewhere on the board
/Level Shift/SCK_IN: JP8.2 (B), JP11.1 (A); also elsewhere on the board
/Level Shift/VPP_EN_CP_IN: U4.11 (PC3); also elsewhere on the board
/Level Shift/nFAULT_OUT: U4.CN7_7 (PB12); also elsewhere on the board
/Level Shift/nFIRE_IN: U4.20 (PE11); also elsewhere on the board
/Level Shift/nRESET_FAULT_OUT: U4.9 (PA3); also elsewhere on the board
/Level Shift/nRESET_OUT: U4.12 (PB1); also elsewhere on the board
/Level Shift/nSS1_IN: U4.19 (PE14); also elsewhere on the board
/Level Shift/nSS2_IN: U4.23 (PG9); also elsewhere on the board
/MCU/STROBE: U4.18 (PE13); also elsewhere on the board
/MCU/nRESET_MCU: U4.13 (PC2); also elsewhere on the board
unnamed: JP3.2 (B), U4.CN7_3 (PB15)
unnamed: JP8.1 (A), U4.28 (PA5)
unnamed: JP9.1 (A), U4.26 (PA7)
unnamed: JP10.2 (B), U4.CN7_13 (PB5)
unnamed: JP11.2 (B), U4.CN7_15 (PB3)
unnamed: JP12.1 (A), U4.21 (PA8)
unnamed: JP13.2 (B), U4.24 (PD15)
unnamed: JP15.1 (A), U4.17 (PG14)
unnamed: JP16.2 (B), U4.CN7_9 (PA15)

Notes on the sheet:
SMPS_PG
SPI
Ethernet
USART

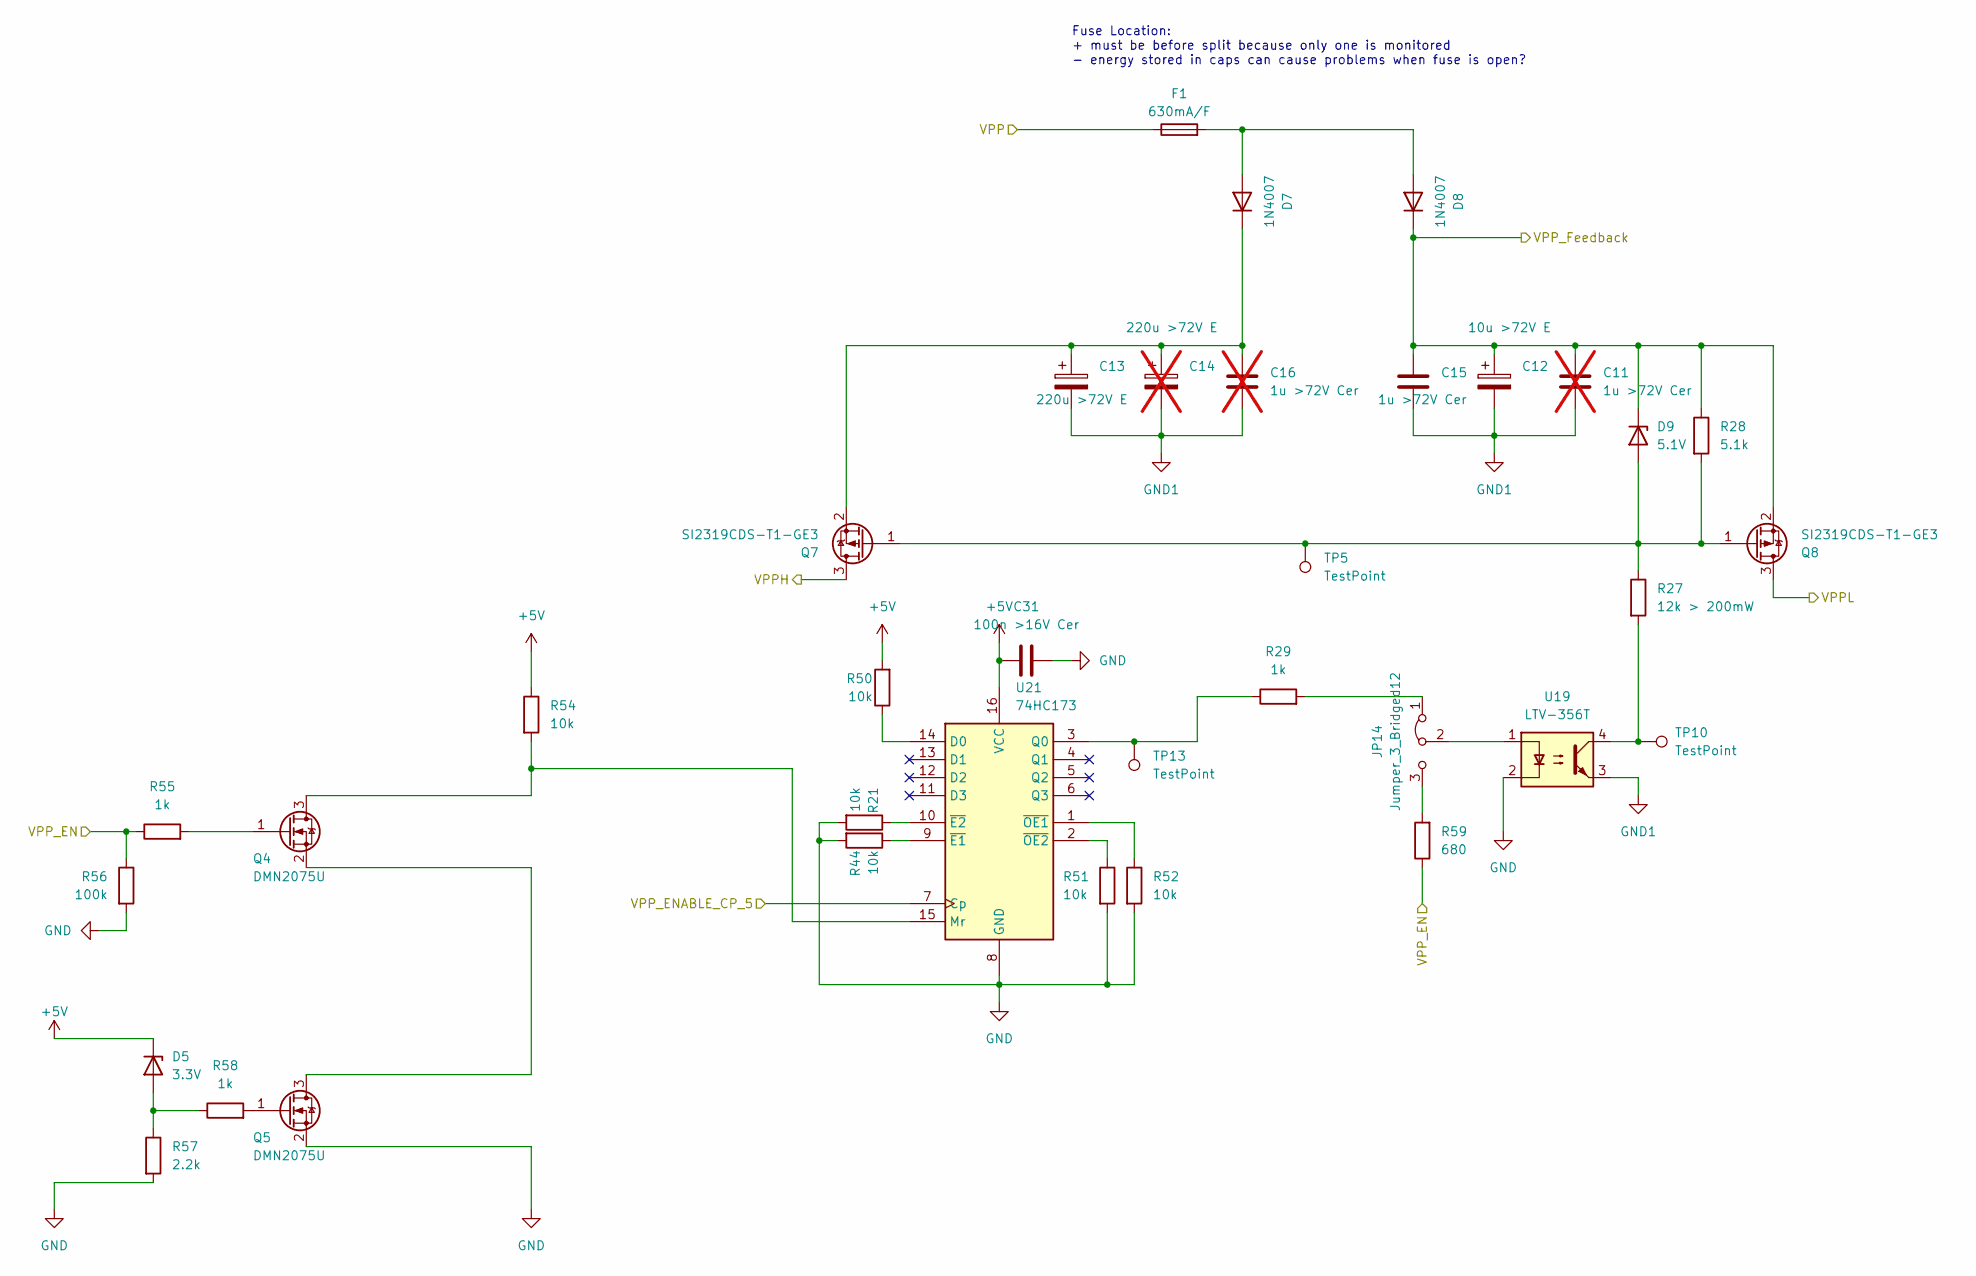
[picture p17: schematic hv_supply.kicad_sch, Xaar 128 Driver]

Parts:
C11, C16: 1u >72V Cer; C_0805_2012Metric_Pad1.18x1.45mm_HandSolder; not fitted
C12: 10u >72V E; CP_Radial_D5.0mm_P2.00mm
C13: 220u >72V E; CP_Radial_D13.0mm_P5.00mm
C14: 220u >72V E; CP_Radial_D13.0mm_P5.00mm; not fitted
C15: 1u >72V Cer; C_0805_2012Metric_Pad1.18x1.45mm_HandSolder
C31: 100n >16V Cer; C_0603_1608Metric_Pad1.08x0.95mm_HandSolder
D5: 3.3V; D_SOD-123F
D7: 1N4007; D_DO-41_SOD81_P10.16mm_Horizontal
D8: 1N4007; D_DO-41_SOD81_P12.70mm_Horizontal
D9: 5.1V; D_DO-35_SOD27_P7.62mm_Horizontal
F1: 630mA/F; FUSE_646_1_LTF
JP14: Jumper_3_Bridged12; PinHeader_1x03_P2.54mm_Vertical
Q4, Q5: DMN2075U; SOT-23
Q7, Q8: SI2319CDS-T1-GE3; SOT-23
R21, R44, R50, R51, R52, R54: 10k; R_0603_1608Metric_Pad0.98x0.95mm_HandSolder
R27: 12k > 200mW; R_1206_3216Metric_Pad1.30x1.75mm_HandSolder
R28: 5.1k; R_0805_2012Metric_Pad1.20x1.40mm_HandSolder
R29, R55, R58: 1k; R_0603_1608Metric_Pad0.98x0.95mm_HandSolder
R56: 100k; R_0603_1608Metric_Pad0.98x0.95mm_HandSolder
R57: 2.2k; R_0603_1608Metric_Pad0.98x0.95mm_HandSolder
R59: 680; R_0603_1608Metric_Pad0.98x0.95mm_HandSolder
TP5, TP10, TP13: TestPoint; TestPoint_Pad_D1.5mm
U19: LTV-356T; SO-4_4.4x3.6mm_P2.54mm
U21: 74HC173; SO-16_3.9x9.9mm_P1.27mm

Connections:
+5V: C31.1, D5.1 (K), R50.2, R54.1, U21.16 (VCC); also elsewhere on the board
/HV Supply/VPP: F1.1; also elsewhere on the board
/HV Supply/VPPH: Q7.3 (D); also elsewhere on the board
/HV Supply/VPPL: Q8.3 (D); also elsewhere on the board
/HV Supply/VPP_EN: R55.1, R56.1, R59.1; also elsewhere on the board
/HV Supply/VPP_ENABLE_CP_5: U21.7 (Cp); also elsewhere on the board
/HV Supply/VPP_Feedback: C11.1, C12.1, C15.1, D8.1 (K), D9.1 (K), Q8.2 (S), R28.1; also elsewhere on the board
unnamed: D5.2 (A), R57.1, R58.1
unnamed: D7.2 (A), D8.2 (A), F1.2
unnamed: C13.1, C14.1, C16.1, D7.1 (K), Q7.2 (S)
unnamed: D9.2 (A), Q7.1 (G), Q8.1 (G), R27.1, R28.2, TP5.1
unnamed: JP14.1 (A), R29.2
unnamed: JP14.3 (B), R59.2
unnamed: JP14.2 (C), U19.1
unnamed: Q4.3 (D), R54.2, U21.15 (Mr)
unnamed: Q4.1 (G), R55.2
unnamed: Q4.2 (S), Q5.3 (D)
unnamed: Q5.1 (G), R58.2
unnamed: R27.2, TP10.1, U19.4
unnamed: R50.1, U21.14 (D0)
unnamed: R29.1, TP13.1, U21.3 (Q0)
unnamed: R44.1, U21.9 (~E1)
unnamed: R21.1, U21.10 (~E2)
unnamed: R52.1, U21.1 (~OE1)
unnamed: R51.1, U21.2 (~OE2)

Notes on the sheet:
Fuse Location: + must be before split because only one is monitored - energy stored in caps can cause problems when fuse is open?

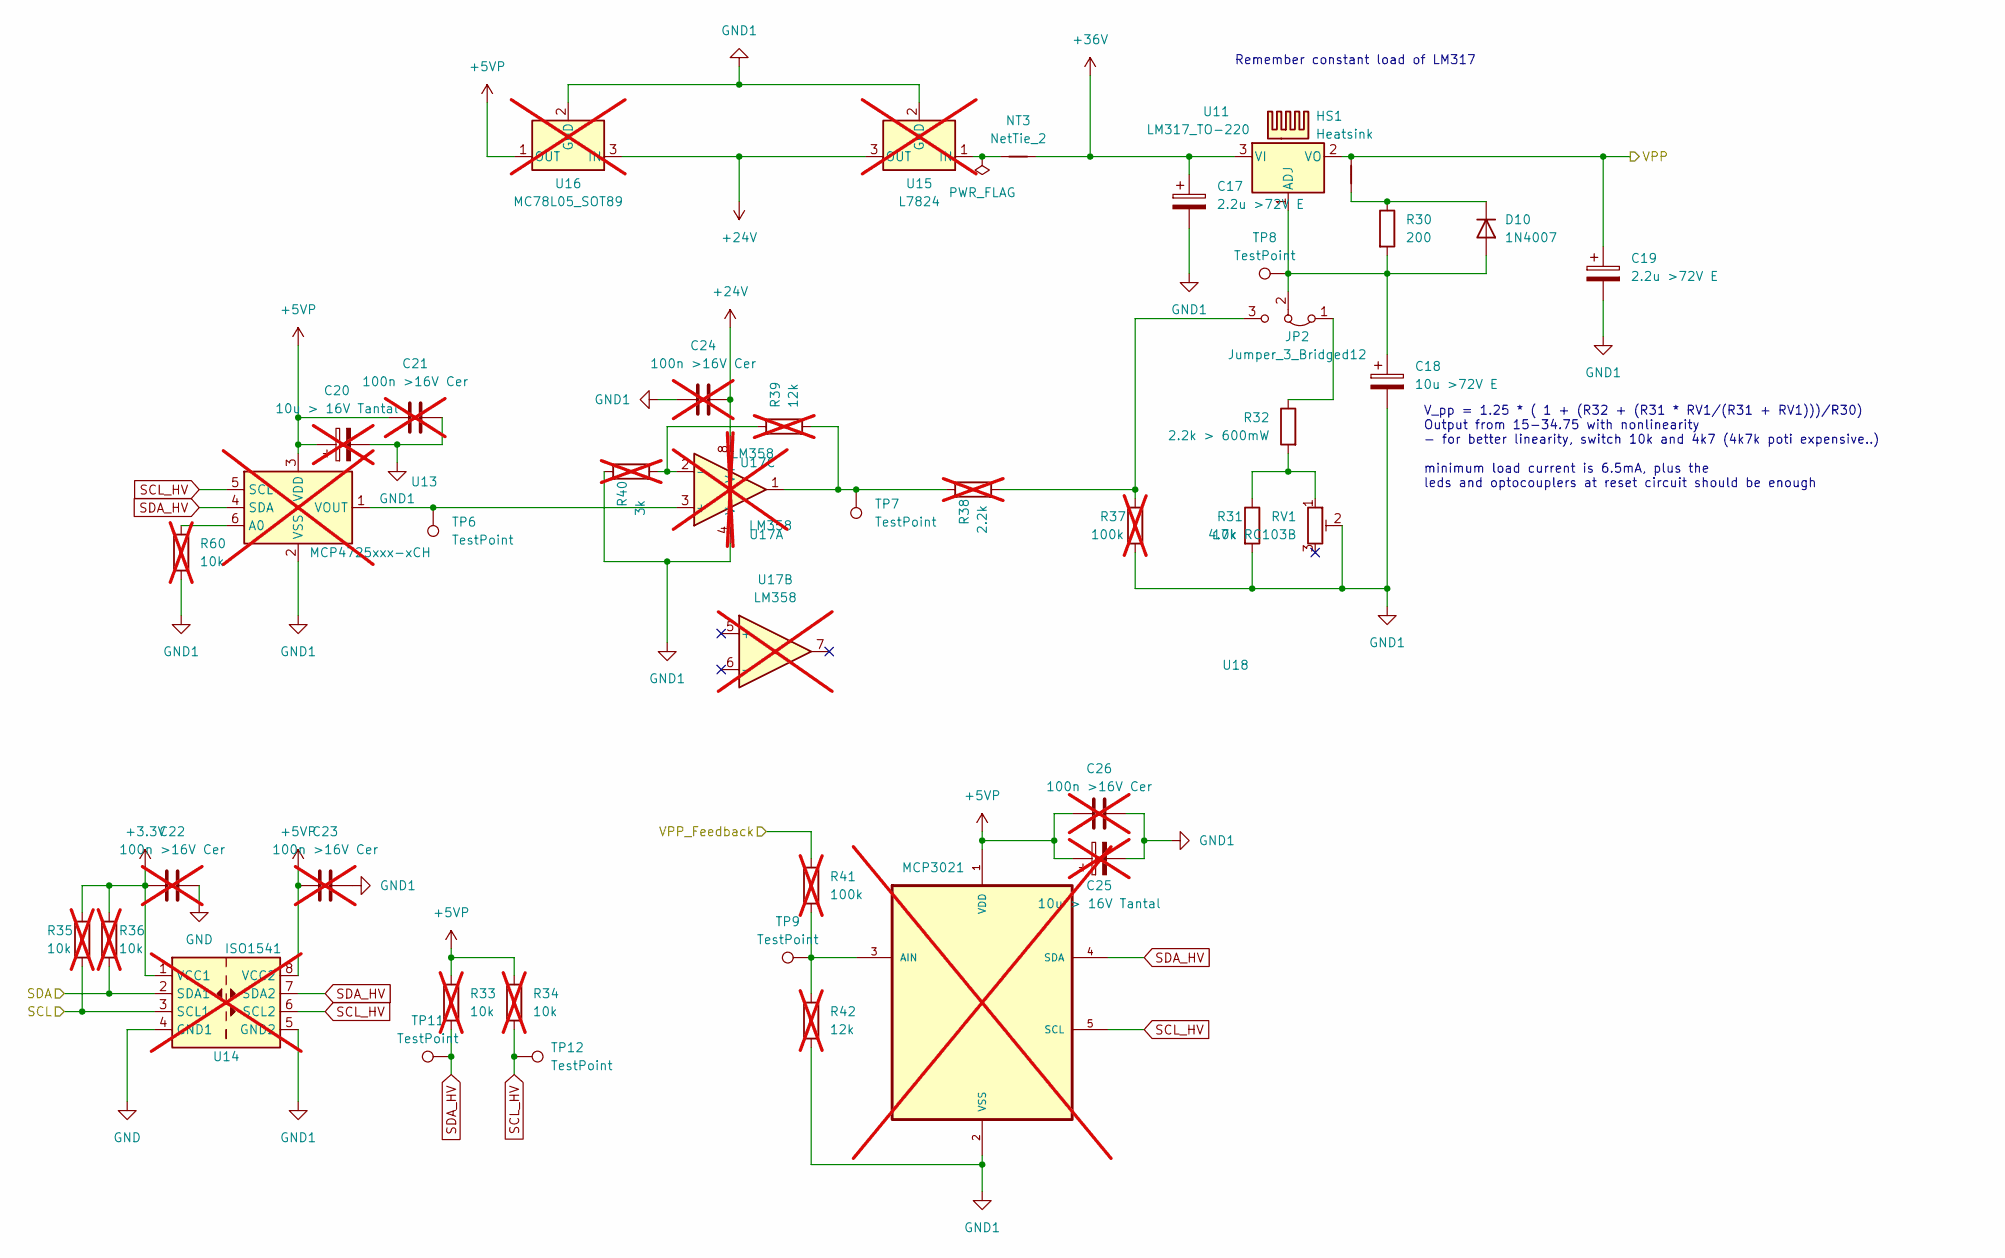
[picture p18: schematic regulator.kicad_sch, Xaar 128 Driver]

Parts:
C17, C19: 2.2u >72V E; CP_Radial_D5.0mm_P2.00mm
C18: 10u >72V E; CP_Radial_D5.0mm_P2.00mm
C20, C25: 10u > 16V Tantal; CP_EIA-3528-21_Kemet-B_Pad1.50x2.35mm_HandSolder; not fitted
C21, C22, C23, C24, C26: 100n >16V Cer; C_0603_1608Metric_Pad1.08x0.95mm_HandSolder; not fitted
D10: 1N4007; D_DO-41_SOD81_P10.16mm_Horizontal
HS1: Heatsink; SK68-375-SA
JP2: Jumper_3_Bridged12; PinHeader_1x03_P2.54mm_Vertical
NT1, NT3: NetTie_2; NetTie-2_SMD_Pad0.5mm
R30: 200; R_Axial_DIN0207_L6.3mm_D2.5mm_P7.62mm_Horizontal
R31: 4.7k; R_0603_1608Metric_Pad0.98x0.95mm_HandSolder
R32: 2.2k > 600mW; R_2512_6332Metric_Pad1.40x3.35mm_HandSolder
R33, R34, R35, R36, R60: 10k; R_0603_1608Metric_Pad0.98x0.95mm_HandSolder; not fitted
R37, R41: 100k; R_0603_1608Metric_Pad0.98x0.95mm_HandSolder; not fitted
R38: 2.2k; R_0603_1608Metric_Pad0.98x0.95mm_HandSolder; not fitted
R39, R42: 12k; R_1206_3216Metric_Pad1.30x1.75mm_HandSolder; not fitted
R40: 3k; R_Axial_DIN0207_L6.3mm_D2.5mm_P7.62mm_Horizontal; not fitted
RV1: 10k RC103B; Potentiometer_Alps_RK09L_Single_Vertical
TP6, TP7, TP8, TP9, TP11, TP12: TestPoint; TestPoint_Pad_D1.5mm
U11: LM317_TO-220; TO-220-3_Vertical
U13: MCP4725xxx-xCH; SOT-23-6_Handsoldering; not fitted
U14: ISO1541; SOIC-8_3.9x4.9mm_P1.27mm; not fitted
U15: L7824; TO-220-3_Vertical; not fitted
U16: MC78L05_SOT89; SOT-89-3; not fitted
U17: LM358; DIP-8_W7.62mm; not fitted
U18: MCP3021; SOT-23-5_HandSoldering; not fitted

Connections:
+5VP: C20.1, C21.1, C23.2, C25.1, C26.1, R33.1, R34.1, U13.3 (VDD), U14.8 (VCC2), U16.1 (OUT), U18.1 (VDD)
+24V: C24.2, U15.3 (OUT), U16.3 (IN), U17.8 (V+)
+36V: C17.1, NT3.2, U11.3 (VI); also elsewhere on the board
/ACC/SCL: R35.2, U14.3 (SCL1); also elsewhere on the board
/ACC/SDA: R36.2, U14.2 (SDA1); also elsewhere on the board
/HV Supply/VPP: C19.1, NT1.1, U11.2 (VO); also elsewhere on the board
/HV Supply/VPP_Feedback: R41.1; also elsewhere on the board
unnamed: C18.1, D10.2 (A), JP2.2 (C), R30.2, TP8.1, U11.1 (ADJ)
unnamed: D10.1 (K), NT1.2, R30.1
unnamed: JP2.1 (A), R32.1
unnamed: JP2.3 (B), R37.1, R38.2
unnamed: R31.1, R32.2, RV1.1
unnamed: R38.1, R39.2, TP7.1, U17.1
unnamed: R60.1, U13.6 (A0)
unnamed: TP6.1, U13.1 (VOUT), U17.3 (+)
unnamed: NT3.1, U15.1 (IN)
unnamed: R39.1, R40.2, U17.2 (-)
unnamed: R41.2, R42.1, TP9.1, U18.3 (AIN)
SCL_HV: R34.2, TP12.1, U13.5 (SCL), U14.6 (SCL2), U18.5 (SCL)
SDA_HV: R33.2, TP11.1, U13.4 (SDA), U14.7 (SDA2), U18.4 (SDA)

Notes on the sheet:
Remember constant load of LM317
V_pp = 1.25 * ( 1 + (R32 + (R31 * RV1/(R31 + RV1)))/R30) Output from 15-34.75 with nonlinearity - for better linearity, switch 10k and 4k7 (4k7k poti expensive..) minimum load current is 6.5mA, plus the leds and optocouplers at reset circuit should be enough

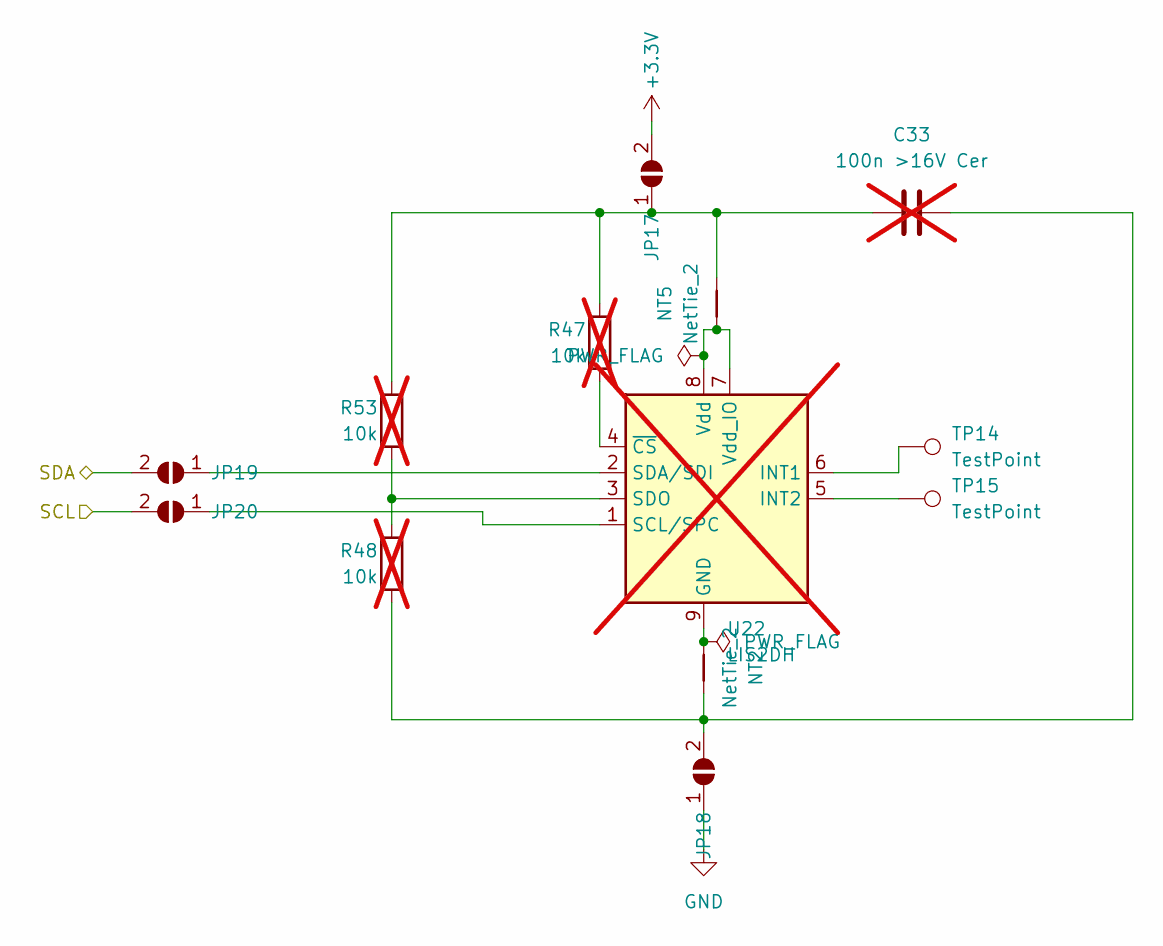
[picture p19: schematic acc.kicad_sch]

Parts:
C33: 100n >16V Cer; C_0603_1608Metric_Pad1.08x0.95mm_HandSolder; not fitted
JP17, JP18, JP19, JP20: SolderJumper_2_Open; R_0603_1608Metric_Pad0.98x0.95mm_HandSolder
NT2, NT5: NetTie_2; NetTie-2_SMD_Pad0.5mm
R47, R48, R53: 10k; R_0603_1608Metric_Pad0.98x0.95mm_HandSolder; not fitted
TP14, TP15: TestPoint; TestPoint_Pad_D1.5mm
U22: LIS2DH; LGA-14_2x2mm_P0.35mm_LayoutBorder3x4y; not fitted

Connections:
/ACC/SCL: JP20.2 (B); also elsewhere on the board
/ACC/SDA: JP19.2 (B); also elsewhere on the board
unnamed: C33.1, JP17.1 (A), NT5.2, R47.2, R53.2
unnamed: C33.2, JP18.2 (B), NT2.2, R48.1
unnamed: JP19.1 (A), U22.2 (SDA/SDI)
unnamed: JP20.1 (A), U22.1 (SCL/SPC)
unnamed: NT2.1, U22.9 (GND), U22.10 (GND), U22.11 (GND), U22.12 (GND), U22.13 (GND), U22.14 (GND)
unnamed: TP14.1, U22.6 (INT1)
unnamed: TP15.1, U22.5 (INT2)
unnamed: R48.2, R53.1, U22.3 (SDO)
unnamed: NT5.1, U22.7 (Vdd_IO), U22.8 (Vdd)
unnamed: R47.1, U22.4 (~CS)

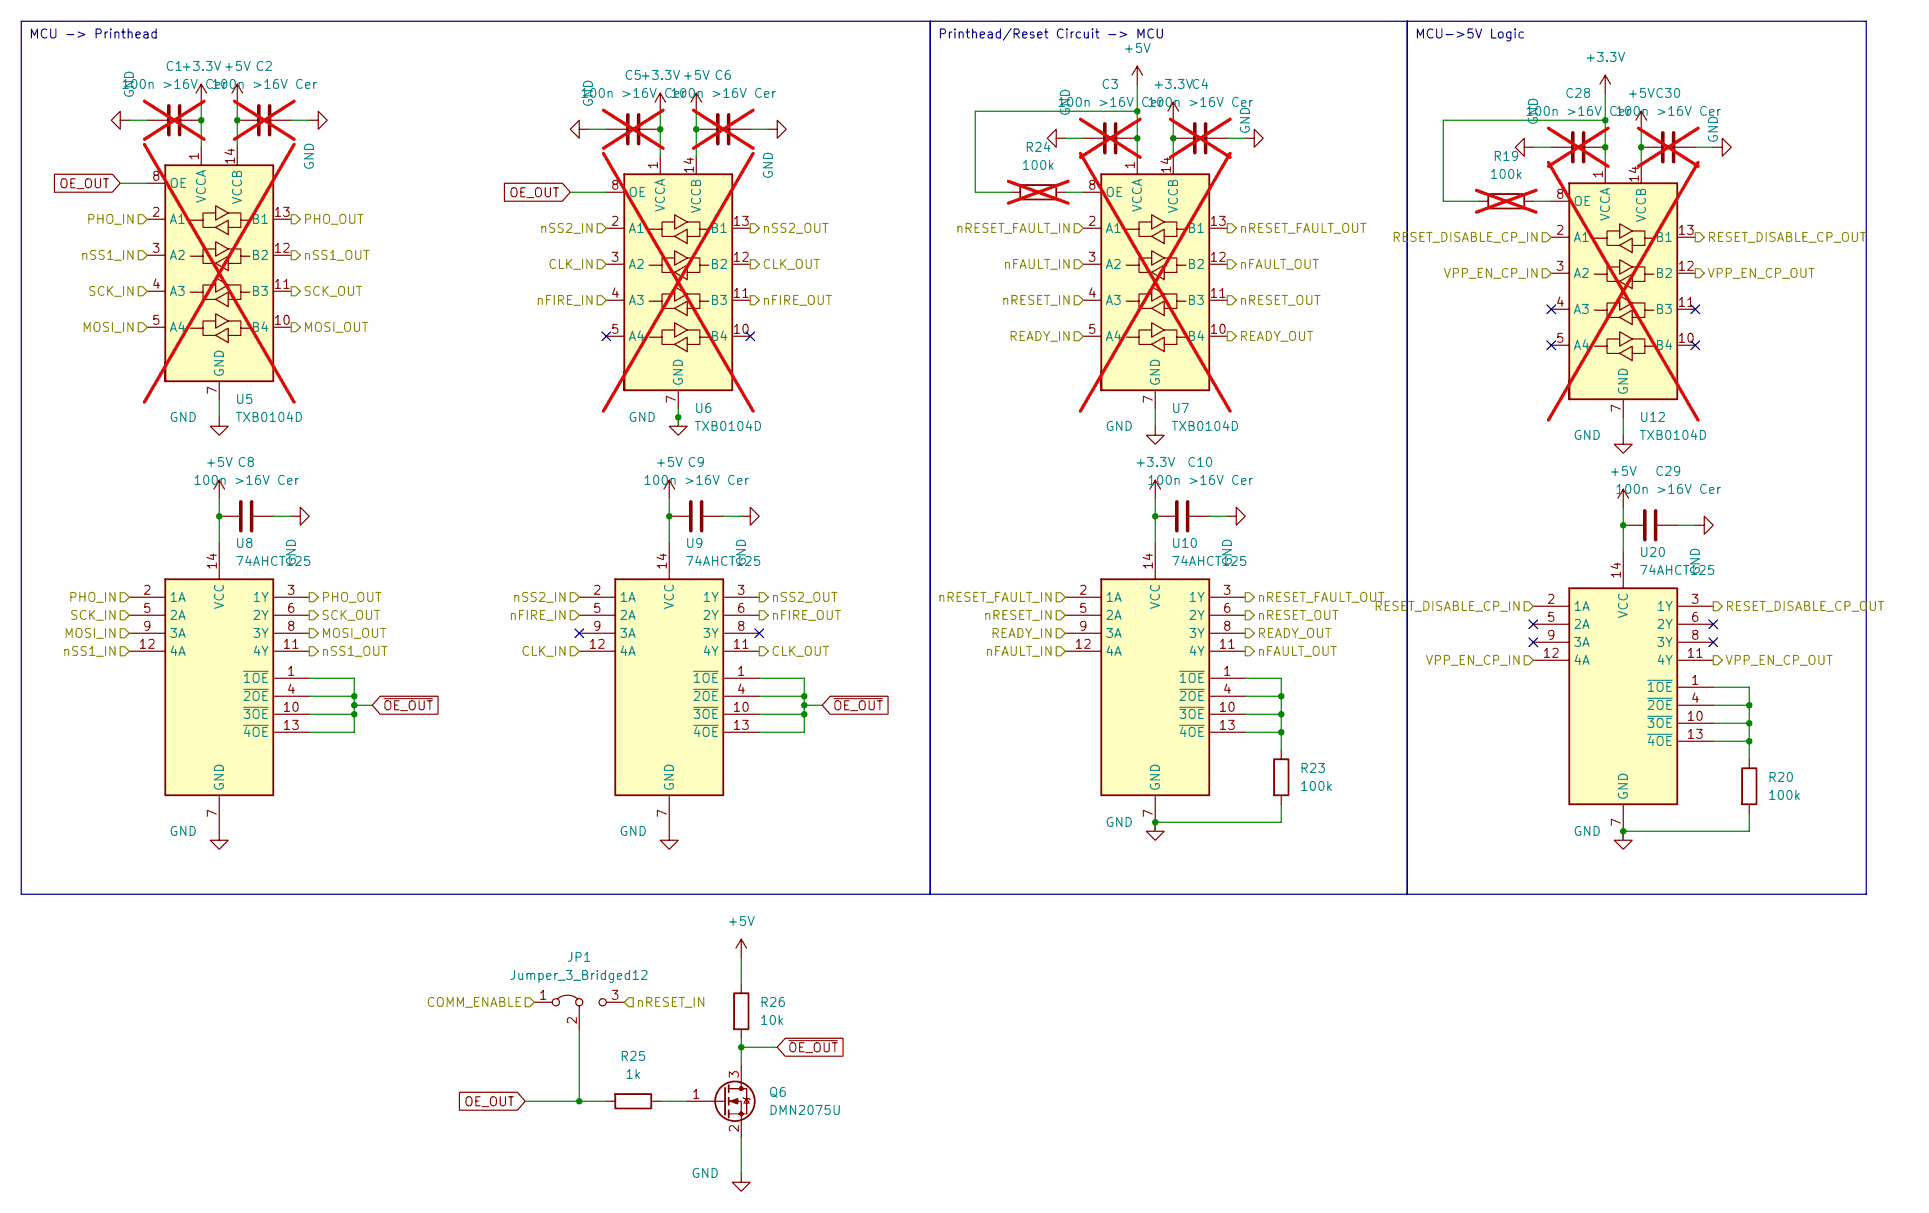
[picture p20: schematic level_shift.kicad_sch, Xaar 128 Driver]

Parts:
C1, C2, C3, C4, C5, C6, C28, C30: 100n >16V Cer; C_0603_1608Metric_Pad1.08x0.95mm_HandSolder; not fitted
C8, C9, C10, C29: 100n >16V Cer; C_0603_1608Metric_Pad1.08x0.95mm_HandSolder
JP1: Jumper_3_Bridged12; PinHeader_1x03_P2.54mm_Vertical
Q6: DMN2075U; SOT-23
R19, R24: 100k; R_0603_1608Metric_Pad0.98x0.95mm_HandSolder; not fitted
R20, R23: 100k; R_0603_1608Metric_Pad0.98x0.95mm_HandSolder
R25: 1k; R_0603_1608Metric_Pad0.98x0.95mm_HandSolder
R26: 10k; R_0603_1608Metric_Pad0.98x0.95mm_HandSolder
U5, U6, U7, U12: TXB0104D; SOIC-14_3.9x8.7mm_P1.27mm; not fitted
U8, U9, U10, U20: 74AHCT125; SOIC-14_3.9x8.7mm_P1.27mm

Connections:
+5V: C2.2, C3.2, C6.2, C8.2, C9.2, C29.2, C30.2, R24.1, R26.1, U5.14 (VCCB), U6.14 (VCCB), U7.1 (VCCA), U8.14 (VCC), U9.14 (VCC), U12.14 (VCCB), U20.14 (VCC); also elsewhere on the board
/HV Supply/VPP_ENABLE_CP_5: U12.12 (B2), U20.11 (4Y); also elsewhere on the board
/IO/nFIRE: U6.11 (B3), U9.6 (2Y); also elsewhere on the board
/Level Shift/CLK_IN: U6.3 (A2), U9.12 (4A); also elsewhere on the board
/Level Shift/CLK_OUT: U6.12 (B2), U9.11 (4Y); also elsewhere on the board
/Level Shift/COMM_ENABLE: JP1.1 (A); also elsewhere on the board
/Level Shift/MOSI_IN: U5.5 (A4), U8.9 (3A); also elsewhere on the board
/Level Shift/MOSI_OUT: U5.10 (B4), U8.8 (3Y); also elsewhere on the board
/Level Shift/PHO_IN: U5.2 (A1), U8.2 (1A); also elsewhere on the board
/Level Shift/PHO_OUT: U5.13 (B1), U8.3 (1Y); also elsewhere on the board
/Level Shift/READY_IN: U7.5 (A4), U10.9 (3A); also elsewhere on the board
/Level Shift/READY_OUT: U7.10 (B4), U10.8 (3Y); also elsewhere on the board
/Level Shift/RESET_DISABLE_CP_IN: U12.2 (A1), U20.2 (1A); also elsewhere on the board
/Level Shift/RESET_DISABLE_CP_OUT: U12.13 (B1), U20.3 (1Y); also elsewhere on the board
/Level Shift/SCK_IN: U5.4 (A3), U8.5 (2A); also elsewhere on the board
/Level Shift/SCK_OUT: U5.11 (B3), U8.6 (2Y); also elsewhere on the board
/Level Shift/VPP_EN_CP_IN: U12.3 (A2), U20.12 (4A); also elsewhere on the board
/Level Shift/nFAULT_IN: U7.3 (A2), U10.12 (4A); also elsewhere on the board
/Level Shift/nFAULT_OUT: U7.12 (B2), U10.11 (4Y); also elsewhere on the board
/Level Shift/nFIRE_IN: U6.4 (A3), U9.5 (2A); also elsewhere on the board
/Level Shift/nRESET_FAULT_IN: U7.2 (A1), U10.2 (1A); also elsewhere on the board
/Level Shift/nRESET_FAULT_OUT: U7.13 (B1), U10.3 (1Y); also elsewhere on the board
/Level Shift/nRESET_IN: JP1.3 (B), U7.4 (A3), U10.5 (2A); also elsewhere on the board
/Level Shift/nRESET_OUT: U7.11 (B3), U10.6 (2Y); also elsewhere on the board
/Level Shift/nSS1_IN: U5.3 (A2), U8.12 (4A); also elsewhere on the board
/Level Shift/nSS1_OUT: U5.12 (B2), U8.11 (4Y); also elsewhere on the board
/Level Shift/nSS2_IN: U6.2 (A1), U9.2 (1A); also elsewhere on the board
/Level Shift/nSS2_OUT: U6.13 (B1), U9.3 (1Y); also elsewhere on the board
unnamed: Q6.1 (G), R25.1
unnamed: R24.2, U7.8 (OE)
unnamed: R23.1, U10.1 (~1OE), U10.4 (~2OE), U10.10 (~3OE), U10.13 (~4OE)
unnamed: R19.2, U12.8 (OE)
unnamed: R20.1, U20.1 (~1OE), U20.4 (~2OE), U20.10 (~3OE), U20.13 (~4OE)
OE_OUT: JP1.2 (C), R25.2, U5.8 (OE), U6.8 (OE)
~OE_OUT: Q6.3 (D), R26.2, U8.1 (~1OE), U8.4 (~2OE), U8.10 (~3OE), U8.13 (~4OE), U9.1 (~1OE), U9.4 (~2OE), U9.10 (~3OE), U9.13 (~4OE)

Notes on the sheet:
MCU->5V Logic
MCU -> Printhead
Printhead/Reset Circuit -> MCU

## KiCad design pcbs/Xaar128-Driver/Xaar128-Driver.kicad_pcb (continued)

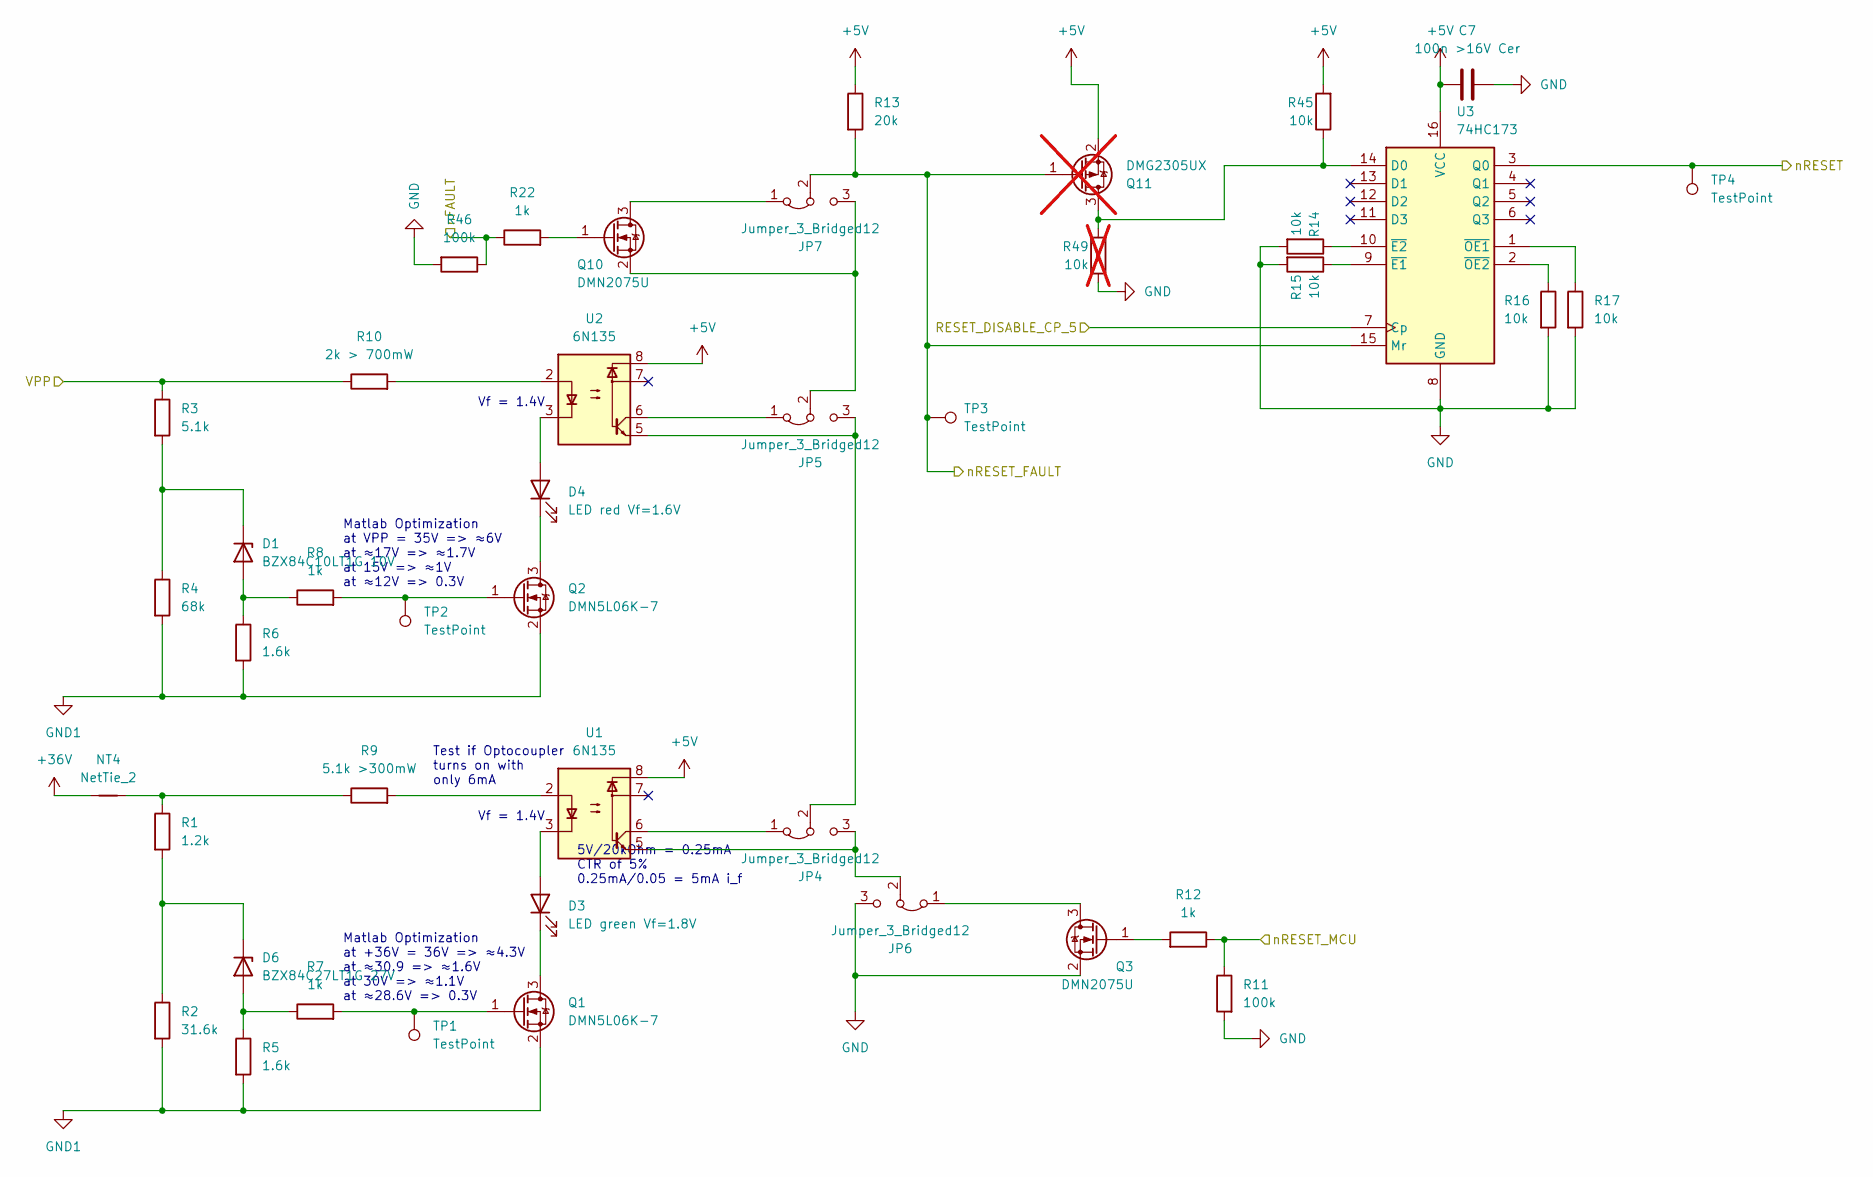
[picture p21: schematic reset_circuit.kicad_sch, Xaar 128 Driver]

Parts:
C7: 100n >16V Cer; C_0603_1608Metric_Pad1.08x0.95mm_HandSolder
D1: BZX84C10LT1G 10V; SOT-23
D3: LED green Vf=1.8V; LED_D5.0mm
D4: LED red Vf=1.6V; LED_D5.0mm
D6: BZX84C27LT1G 27V; SOT-23
JP4, JP5, JP6, JP7: Jumper_3_Bridged12; PinHeader_1x03_P2.54mm_Vertical
NT4: NetTie_2; NetTie-2_SMD_Pad0.5mm
Q1, Q2: DMN5L06K-7; SOT-23
Q3, Q10: DMN2075U; SOT-23
Q11: DMG2305UX; SOT-23; not fitted
R1: 1.2k; R_0603_1608Metric_Pad0.98x0.95mm_HandSolder
R2: 31.6k; R_0603_1608Metric_Pad0.98x0.95mm_HandSolder
R3: 5.1k; R_0805_2012Metric_Pad1.20x1.40mm_HandSolder
R4: 68k; R_0603_1608Metric_Pad0.98x0.95mm_HandSolder
R5, R6: 1.6k; R_0603_1608Metric_Pad0.98x0.95mm_HandSolder
R7, R8, R12, R22: 1k; R_0603_1608Metric_Pad0.98x0.95mm_HandSolder
R9: 5.1k >300mW; R_0805_2012Metric_Pad1.20x1.40mm_HandSolder
R10: 2k > 700mW; R_2010_5025Metric_Pad1.40x2.65mm_HandSolder
R11, R46: 100k; R_0603_1608Metric_Pad0.98x0.95mm_HandSolder
R13: 20k; R_0603_1608Metric_Pad0.98x0.95mm_HandSolder
R14, R15, R16, R17, R45: 10k; R_0603_1608Metric_Pad0.98x0.95mm_HandSolder
R49: 10k; R_0603_1608Metric_Pad0.98x0.95mm_HandSolder; not fitted
TP1, TP2, TP3, TP4: TestPoint; TestPoint_Pad_D1.5mm
U1, U2: 6N135; DIP-8_W7.62mm
U3: 74HC173; SO-16_3.9x9.9mm_P1.27mm

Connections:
+5V: C7.1, Q11.2 (S), R13.1, R45.2, U1.8, U2.8, U3.16 (VCC); also elsewhere on the board
+36V: NT4.1; also elsewhere on the board
/HV Supply/VPPL: R3.1, R10.1; also elsewhere on the board
/Level Shift/RESET_DISABLE_CP_OUT: U3.7 (Cp); also elsewhere on the board
/Level Shift/nFAULT_IN: R22.1, R46.1; also elsewhere on the board
/Level Shift/nRESET_FAULT_IN: JP7.2 (C), Q11.1 (G), R13.2, TP3.1, U3.15 (Mr); also elsewhere on the board
/Level Shift/nRESET_IN: TP4.1, U3.3 (Q0); also elsewhere on the board
/MCU/nRESET_MCU: R11.1, R12.1; also elsewhere on the board
unnamed: D1.1 (A), R6.1, R8.1
unnamed: D1.3 (K), R3.2, R4.1
unnamed: D3.2 (A), U1.3
unnamed: D3.1 (K), Q1.3 (D)
unnamed: D4.2 (A), U2.3
unnamed: D4.1 (K), Q2.3 (D)
unnamed: D6.1 (A), R5.1, R7.1
unnamed: JP4.1 (A), U1.6
unnamed: JP4.3 (B), JP6.2 (C), U1.5
unnamed: JP4.2 (C), JP5.3 (B), U2.5
unnamed: JP5.1 (A), U2.6
unnamed: JP5.2 (C), JP7.3 (B), Q10.2 (S)
unnamed: JP6.1 (A), Q3.3 (D)
unnamed: JP7.1 (A), Q10.3 (D)
unnamed: NT4.2, R1.1, R9.1
unnamed: Q1.1 (G), R7.2, TP1.1
unnamed: Q2.1 (G), R8.2, TP2.1
unnamed: Q3.1 (G), R12.2
unnamed: Q10.1 (G), R22.2
unnamed: Q11.3 (D), R45.1, R49.2, U3.14 (D0)
unnamed: R9.2, U1.2
unnamed: R10.2, U2.2
unnamed: R15.1, U3.9 (~E1)
unnamed: R14.1, U3.10 (~E2)
unnamed: R17.1, U3.1 (~OE1)
unnamed: R16.1, U3.2 (~OE2)

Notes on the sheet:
Vf = 1.4V
5V/20kOhm = 0.25mA CTR of 5% 0.25mA/0.05 = 5mA i_f
Test if Optocoupler turns on with only 6mA
Matlab Optimization at +36V = 36V => ≈4.3V at ≈30.9 => ≈1.6V at 30V => ≈1.1V at ≈28.6V => 0.3V
Matlab Optimization at VPP = 35V => ≈6V at ≈17V => ≈1.7V at 15V => ≈1V at ≈12V => 0.3V

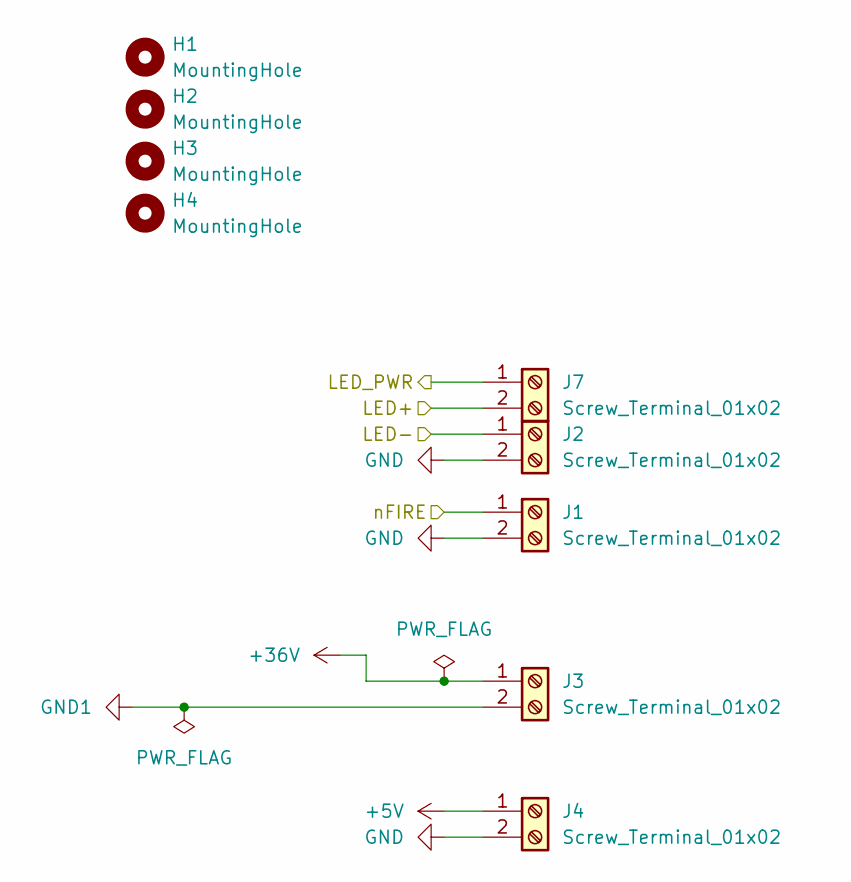
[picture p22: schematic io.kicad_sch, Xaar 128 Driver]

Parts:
H1, H2, H3, H4: MountingHole; MountingHole_2.7mm_M2.5_DIN965
J1, J2, J3, J4, J7: Screw_Terminal_01x02; 897-1051

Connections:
+5V: J4.1; also elsewhere on the board
+36V: J3.1; also elsewhere on the board
/IO/LED+: J7.2; also elsewhere on the board
/IO/LED-: J2.1; also elsewhere on the board
/IO/LED_PWR: J7.1; also elsewhere on the board
/IO/nFIRE: J1.1; also elsewhere on the board

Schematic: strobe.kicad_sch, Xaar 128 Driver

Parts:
C1: 100n >16V Film; C_Rect_L7.0mm_W3.5mm_P5.00mm
NT7: NetTie_2; NetTie-2_SMD_Pad0.5mm
Q9: DMN2075U; SOT-23
R2: 10k; R_0603_1608Metric_Pad0.98x0.95mm_HandSolder

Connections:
/IO/LED+: NT7.2; also elsewhere on the board
/IO/LED-: Q9.3 (D); also elsewhere on the board
/IO/LED_PWR: NT7.1; also elsewhere on the board

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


Board: 2 copper layers, 100.0 x 100.0 mm, 188 parts (132 on the bottom side), 131 nets.

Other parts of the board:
C27: 100n >16V Film; C_Rect_L7.0mm_W3.5mm_P5.00mm
R43: 10k; R_0603_1608Metric_Pad0.98x0.95mm_HandSolder

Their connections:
/MCU/STROBE: C27.1; also elsewhere on the board

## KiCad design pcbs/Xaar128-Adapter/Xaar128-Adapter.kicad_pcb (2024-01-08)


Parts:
D1: LED yellow Vf=1.6V; LED_D3.0mm
D2: LED green Vf=1.8V; LED_D3.0mm
H1, H2: MountingHole; MountingHole_2.7mm_M2.5_DIN965
J1: Conn_01x21; Molex_200528-0210_1x21-1MP_P1.00mm_Horizontal
J2: Conn_02x15_Odd_Even; CONN_9-176140-0_TYC
J3: Conn_01x12; Molex_52207-1260_1x12-1MP_P1.00mm_Horizontal; not fitted
NT1, NT2: NetTie_2; NetTie-2_SMD_Pad0.5mm
Q1: DMN2075U; SOT-23
R1: 0; R_0603_1608Metric_Pad0.98x0.95mm_HandSolder
R2: 10K; R_0603_1608Metric_Pad0.98x0.95mm_HandSolder; not fitted
R3: 1k; R_0603_1608Metric_Pad0.98x0.95mm_HandSolder
R4: 470; R_0603_1608Metric_Pad0.98x0.95mm_HandSolder
R6: 5.1k >300mW; R_0805_2012Metric_Pad1.20x1.40mm_HandSolder

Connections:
+5V: J1.12, J2.17, R1.1, R4.2
/MISO: J2.27
CLK: J1.3, J2.28
GND: J1.2, J1.4, J1.8, J1.10, J1.13, J1.15, J2.16, J3.12, Q1.2 (S), R2.1
GNDH: J1.20, J2.2, J2.30, NT2.1
GNDL: J1.18, J2.5
MOSI: J1.14, J2.8
unnamed: D1.2 (A), R4.1
unnamed: D1.1 (K), Q1.3 (D)
unnamed: D2.2 (A), R6.1
unnamed: D2.1 (K), NT2.2
unnamed: NT1.1, R6.2
unnamed: Q1.1 (G), R3.1
PHO: J1.6, J2.25
READY: J1.7, J2.24
SCK: J1.11, J2.19
TEST_0: J2.9, J3.1
TEST_1: J2.10, J3.2
TEST_2: J2.11, J3.3
TEST_3: J2.12, J3.4
TEST_4: J2.13, J3.5
TEST_5: J2.14, J3.6
TEST_6: J2.15, J3.7
TEST_7: J2.21, J3.9
TEST_8: J2.22, J3.10
TEST_9: J2.23, J3.11
TEST_10: J2.18, J3.8, R1.2
VPPH: J1.21, J2.3, J2.29, NT1.2
VPPL: J1.19, J2.4
nFAULT: J1.17, J2.6
nFIRE: J1.5, J2.26
nRESET: J1.16, J2.7, R2.2, R3.2
nSS1: J1.9, J2.20
nSS2: J1.1, J2.1

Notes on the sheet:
min pin height: 3mm insert depth: 2mm



Board: 2 copper layers, 41.0 x 38.0 mm, 15 parts (11 on the bottom side), 33 nets.

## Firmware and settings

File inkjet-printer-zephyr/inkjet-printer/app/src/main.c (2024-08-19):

#include <zephyr/kernel.h>
#include <zephyr/drivers/printer.h>
#include <zephyr/drivers/printer_fire.h>
#include <app_version.h>
#include <zephyr/kernel.h>
#include <zephyr/device.h>
#include <zephyr/drivers/gpio.h>
#include <zephyr/sys/util.h>
#include <zephyr/sys/printk.h>
#include <inttypes.h>
#include <zephyr/logging/log.h>
#include <zephyr/shell/shell.h>
#include <zephyr/console/console.h>
#include <stdlib.h>
#include <zephyr/drivers/sensor.h>
#include <zephyr/drivers/motor.h>
#include <zephyr/drivers/pwm.h>

#include "pressure_control.h"
#include "printhead_routines.h"
#include "printer_system_smf.h"
#include "failure_handling.h"
#include "print_control.h"
#include "regulator.h"

LOG_MODULE_REGISTER(main, CONFIG_APP_LOG_LEVEL);
#define SW0_NODE DT_ALIAS(sw0)
#if !DT_NODE_HAS_STATUS(SW0_NODE, okay)
#error "Unsupported board: sw0 devicetree alias is not defined"
#endif

static const struct gpio_dt_spec button = GPIO_DT_SPEC_GET_OR(SW0_NODE, gpios,
															  {0});
static struct gpio_callback button_cb_data;

static const struct gpio_dt_spec vpp_en = GPIO_DT_SPEC_GET(DT_NODELABEL(vpp_en), gpios);
static const struct gpio_dt_spec comm_enable = GPIO_DT_SPEC_GET(DT_NODELABEL(comm_enable), gpios);
static const struct gpio_dt_spec vpp_enable_cp = GPIO_DT_SPEC_GET(DT_NODELABEL(vpp_enable_cp), gpios);

static const struct gpio_dt_spec n_reset_fault = GPIO_DT_SPEC_GET(DT_NODELABEL(n_reset_fault), gpios);
static const struct gpio_dt_spec n_reset_in = GPIO_DT_SPEC_GET(DT_NODELABEL(n_reset_in), gpios);

static struct gpio_dt_spec nSS2 = GPIO_DT_SPEC_GET(DT_NODELABEL(nss2), gpios);
static struct gpio_dt_spec nSS1 = GPIO_DT_SPEC_GET(DT_NODELABEL(nss1), gpios);
static struct gpio_dt_spec PHO = GPIO_DT_SPEC_GET(DT_NODELABEL(pho), gpios);

static struct gpio_dt_spec nFAULT = GPIO_DT_SPEC_GET(DT_NODELABEL(nfault), gpios);
static struct gpio_dt_spec READY = GPIO_DT_SPEC_GET(DT_NODELABEL(ready), gpios);

static struct gpio_callback READY_cb_data;

void encoder_debug_timer_handler(struct k_timer *timer)
{
	const struct device *const dev = DEVICE_DT_GET(DT_NODELABEL(qdec));
	if (!device_is_ready(dev))
	{
		printk("Qdec device is not ready\n");
		return;
	}
	struct sensor_value val;
	int rc = sensor_sample_fetch(dev);
	rc = sensor_channel_get(dev, SENSOR_CHAN_POS_DX, &val);
	if (rc != 0)
	{
		printk("Failed to get data (%d)\n", rc);
		return;
	}
	printk("Encoder value: %d\n", val.val1);
}

void pressure_debug_timer_handler(struct k_timer *timer)
{
	double pressure = pressure_control_get_pressure();
	printk("Pressure: %f mbar\n", pressure);
}
static int fire_count = 0;
static int drop_count = 100;

void print_fire_timer_handler(struct k_timer *timer);

K_TIMER_DEFINE(pressure_debug_timer, pressure_debug_timer_handler, NULL);

K_TIMER_DEFINE(print_fire_timer, print_fire_timer_handler, NULL);

K_TIMER_DEFINE(encoder_debug_timer, encoder_debug_timer_handler, NULL);

static uint32_t pattern[4] = {0, 0, 0, 1};

static void advance_pattern()
{
	bool filling = (pattern[3] & 0x80000000) == 0;
	for (int i = 3; i >= 0; i--)
	{
		pattern[i] = (pattern[i] << 1);
		if (i > 0 && (pattern[i - 1] & 0x80000000))
		{
			pattern[i] |= 1;
		}
	}
	if (pattern[3] & 0x80000000)
	{
		pattern[0] |= 1;
	}
	// if (filling)
	// {
	// 	pattern[0] |= 1;
	// }
}

void print_fire_timer_handler(struct k_timer *timer)
{
	if (gpio_pin_get_dt(&READY) == 1)
	{
		// if (fire_count % 30 == 0)
		// {
		// 	advance_pattern();
		// }
		const struct device *printhead = DEVICE_DT_GET(DT_NODELABEL(printhead));
		// printer_set_pixels(printhead, pattern);
		request_printhead_fire();
	}
	fire_count++;
	if (fire_count > drop_count)
	{
		k_timer_stop(&print_fire_timer);
		fire_count = 0;
	}
}

K_EVENT_DEFINE(btn_event);

void button_pressed(const struct device *dev, struct gpio_callback *cb,
					uint32_t pins)
{
	failure_handling_set_error_state(ERROR_USER_ABORT);
}

void READY_int_handler(const struct device *dev, struct gpio_callback *cb,
					   uint32_t pins)
{
	LOG_INF("READY changed to %d", gpio_pin_get_dt(&READY));
}

static int printhead_io_init()
{
	int ret;
	if (!gpio_is_ready_dt(&nSS2))
	{
		LOG_ERR("Error: nSS2 device %s is not ready\n",
				nSS2.port->name);
		return ENODEV;
	}
	ret = gpio_pin_configure_dt(&nSS2, GPIO_OUTPUT_INACTIVE);
	if (ret != 0)
	{
		LOG_ERR("Error %d: failed to configure %s pin %d\n",
				ret, nSS2.port->name, nSS2.pin);
		return ret;
	}
	if (!gpio_is_ready_dt(&nSS1))
	{
		LOG_ERR("Error: nSS1 device %s is not ready\n",
				nSS1.port->name);
		return ENODEV;
	}
	ret = gpio_pin_configure_dt(&nSS1, GPIO_OUTPUT_INACTIVE);
	if (ret != 0)
	{
		LOG_ERR("Error %d: failed to configure %s pin %d\n",
				ret, nSS1.port->name, nSS1.pin);
		return ret;
	}
	if (!gpio_is_ready_dt(&PHO))
	{
		LOG_ERR("Error: PHO device %s is not ready\n",
				PHO.port->name);
		return ENODEV;
	}
	ret = gpio_pin_configure_dt(&PHO, GPIO_OUTPUT_INACTIVE);
	if (ret != 0)
	{
		LOG_ERR("Error %d: failed to configure %s pin %d\n",
				ret, PHO.port->name, PHO.pin);
		return ret;
	}
	if (!gpio_is_ready_dt(&READY))
	{
		LOG_ERR("Error: READY device %s is not ready\n",
				READY.port->name);
		return ENODEV;
	}
	ret = gpio_pin_configure_dt(&READY, GPIO_INPUT);
	if (ret != 0)
	{
		LOG_ERR("Error %d: failed to configure %s pin %d\n",
				ret, READY.port->name, READY.pin);
		return ret;
	}
	ret = gpio_pin_interrupt_configure_dt(&READY,
										  GPIO_INT_EDGE_BOTH);
	if (ret != 0)
	{
		LOG_ERR("Error %d: failed to configure interrupt on %s pin %d\n",
				ret, READY.port->name, READY.pin);
		return ret;
	}
	gpio_init_callback(&READY_cb_data, READY_int_handler, BIT(READY.pin));
	ret = gpio_add_callback(READY.port, &READY_cb_data);
	if (ret != 0)
	{
		LOG_ERR("Error %d: failed to add callback on %s pin %d\n",
				ret, READY.port->name, READY.pin);
		return ret;
	}
	return 0;
}

int initialize_io()
{
	int ret;
	ret = printhead_io_init();
	if (ret != 0)
	{
		return ret;
	}
	return 0;
}

static int shell_wait(const struct shell *sh)
{
	int32_t events;
	shell_print(sh, "Press button to continue.");
	k_event_clear(&btn_event, 0x1);
	events = k_event_wait_all(&btn_event, 0x1, false, K_SECONDS(20));
	if (events == 0)
	{
		shell_print(sh, "Timeout");
		return ETIMEDOUT;
	}
	return 0;
}

static int cmd_test_hv_supply(const struct shell *sh, size_t argc, char **argv)
{
	ARG_UNUSED(argc);
	ARG_UNUSED(argv);

	shell_print(sh, "Disconnect HV supply, discharge capacitor, confirm 0V on printhead connector VPPH and VPPL.");
	if (shell_wait(sh) == ETIMEDOUT)
	{
		return ETIMEDOUT;
	}
	shell_print(sh, "Connect HV supply, confirm 0V on printhead connector VPPH and VPPL.");
	if (shell_wait(sh) == ETIMEDOUT)
	{
		return ETIMEDOUT;
	}
	gpio_pin_set_dt(&vpp_en, 1);
	shell_print(sh, "Confirm again 0V on VPPH and VPPL.");
	if (shell_wait(sh) == ETIMEDOUT)
	{
		return ETIMEDOUT;
	}
	gpio_pin_set_dt(&vpp_enable_cp, 1);
	k_sleep(K_MSEC(1));
	gpio_pin_set_dt(&vpp_enable_cp, 0);
	shell_print(sh, "Confirm VPPH and VPPL active.");
	if (shell_wait(sh) == ETIMEDOUT)
	{
		return ETIMEDOUT;
	}
	gpio_pin_set_dt(&vpp_en, 0);
	shell_print(sh, "Confirm again 0V on VPPH and VPPL.");
	if (shell_wait(sh) == ETIMEDOUT)
	{
		return ETIMEDOUT;
	}
	shell_print(sh, "done");
	return 0;
}

static int cmd_test_printhead_io(const struct shell *sh, size_t argc, char **argv)
{
	ARG_UNUSED(argc);
	ARG_UNUSED(argv);

	gpio_pin_set_dt(&nSS2, 1);
	gpio_pin_set_dt(&nSS1, 1);
	gpio_pin_set_dt(&PHO, 0);
	gpio_pin_set_dt(&comm_enable, 1);
	shell_print(sh, "Connect nSS2 to READY");
	if (shell_wait(sh) == ETIMEDOUT)
	{
		return ETIMEDOUT;
	}
	if (gpio_pin_get_dt(&READY) != 0)
	{
		shell_print(sh, "READY is not low");
		return EINVAL;
	}
	gpio_pin_set_dt(&nSS2, 0);
	k_sleep(K_MSEC(1));
	if (gpio_pin_get_dt(&READY) != 1)
	{
		shell_print(sh, "READY is not high");
		return EINVAL;
	}
	gpio_pin_set_dt(&nSS2, 1);
	shell_print(sh, "Connect nSS1 to READY");
	if (shell_wait(sh) == ETIMEDOUT)
	{
		return ETIMEDOUT;
	}
	if (gpio_pin_get_dt(&READY) != 0)
	{
		shell_print(sh, "READY is not low");
		return EINVAL;
	}
	gpio_pin_set_dt(&nSS1, 0);
	k_sleep(K_MSEC(1));
	if (gpio_pin_get_dt(&READY) != 1)
	{
		shell_print(sh, "READY is not high");
		return EINVAL;
	}
	gpio_pin_set_dt(&nSS1, 1);
	shell_print(sh, "Connect PHO to nFAULT");
	if (shell_wait(sh) == ETIMEDOUT)
	{
		return ETIMEDOUT;
	}
	if (gpio_pin_get_dt(&nFAULT) != 0)
	{
		shell_print(sh, "nFAULT is not low");
		return EINVAL;
	}
	gpio_pin_set_dt(&PHO, 1);
	k_sleep(K_MSEC(1));
	if (gpio_pin_get_dt(&nFAULT) != 1)
	{
		shell_print(sh, "nFAULT is not high");
		return EINVAL;
	}
	gpio_pin_set_dt(&PHO, 0);
	shell_print(sh, "done");
	return 0;
}

static int cmd_test_other_io(const struct shell *sh, size_t argc, char **argv)
{
	ARG_UNUSED(argc);
	ARG_UNUSED(argv);
	gpio_pin_set_dt(&comm_enable, 0);
	shell_print(sh, "Connect COMM_ENABLE to nRESET_FAULT");
	if (shell_wait(sh) == ETIMEDOUT)
	{
		return ETIMEDOUT;
	}
	if (gpio_pin_get_dt(&n_reset_fault) != 0)
	{
		shell_print(sh, "nRESET_FAULT is not low");
		return EINVAL;
	}
	gpio_pin_set_dt(&comm_enable, 1);
	k_sleep(K_MSEC(1));
	if (gpio_pin_get_dt(&n_reset_fault) != 1)
	{
		shell_print(sh, "nRESET_FAULT is not high");
		return EINVAL;
	}
	gpio_pin_set_dt(&comm_enable, 0);
	shell_print(sh, "Connect COMM_ENABLE to nRESET_IN");
	if (shell_wait(sh) == ETIMEDOUT)
	{
		return ETIMEDOUT;
	}
	if (gpio_pin_get_dt(&n_reset_in) != 0)
	{
		shell_print(sh, "nRESET_IN is not low");
		return EINVAL;
	}
	gpio_pin_set_dt(&comm_enable, 1);
	k_sleep(K_MSEC(1));
	if (gpio_pin_get_dt(&n_reset_in) != 1)
	{
		shell_print(sh, "nRESET_IN is not high");
		return EINVAL;
	}
	gpio_pin_set_dt(&comm_enable, 0);
	shell_print(sh, "done");
	return 0;
}

static int cmd_set_pixels(const struct shell *sh, size_t argc, char **argv)
{
	if (argc != 5)
	{
		shell_print(sh, "Usage: set_pixels <pixels1> <pixels2> <pixels3> <pixels4>");
		return EINVAL;
	}
	uint32_t pixels[4] = {(uint32_t)strtoll(argv[1], NULL, 16), (uint32_t)strtoll(argv[2], NULL, 16), (uint32_t)strtoll(argv[3], NULL, 16), (uint32_t)strtoll(argv[4], NULL, 16)};
	shell_print(sh, "Setting pixels to %d %d %d %d", pixels[0], pixels[1], pixels[2], pixels[3]);
	k_sleep(K_SECONDS(1));
	const struct device *printhead;
	printhead = DEVICE_DT_GET(DT_NODELABEL(printhead));

	return printer_set_pixels(printhead, pixels);
}

static int cmd_comm_enable(const struct shell *sh, size_t argc, char **argv)
{
	if (argc != 2)
	{
		shell_print(sh, "Usage: comm_enable <0|1>");
		return EINVAL;
	}
	int value = atoi(argv[1]);
	if (value != 0 && value != 1)
	{
		shell_print(sh, "Usage: comm_enable <0|1>");
		return EINVAL;
	}
	gpio_pin_set_dt(&comm_enable, value);
	return 0;
}

static int cmd_pressure_control_enable(const struct shell *sh, size_t argc, char **argv, void *data)
{
	ARG_UNUSED(argc);
	ARG_UNUSED(argv);
	bool enable = (bool)data;
	if (enable)
	{
		pressure_control_enable();
	}
	else
	{
		pressure_control_disable();
	}
	return 0;
}

SHELL_SUBCMD_DICT_SET_CREATE(pressure_control_enable_cmds, cmd_pressure_control_enable,
							 (enable, true, "enable"), (disable, false, "disable"));

static int cmd_pressure_control_print_pressure(const struct shell *sh, size_t argc, char **argv, void *data)
{
	ARG_UNUSED(argc);
	ARG_UNUSED(argv);
	bool enable = (bool)data;
	if (enable)
	{
		k_timer_start(&pressure_debug_timer, K_SECONDS(1), K_SECONDS(1));
	}
	else
	{
		k_timer_stop(&pressure_debug_timer);
	}
	return 0;
}

SHELL_SUBCMD_DICT_SET_CREATE(pressure_control_print_pressure_cmds, cmd_pressure_control_print_pressure,
							 (enable, true, "enable"), (disable, false, "disable"));

static int cmd_encoder_print(const struct shell *sh, size_t argc, char **argv, void *data)
{
	ARG_UNUSED(argc);
	ARG_UNUSED(argv);
	bool enable = (bool)data;
	if (enable)
	{
		k_timer_start(&encoder_debug_timer, K_SECONDS(1), K_SECONDS(1));
	}
	else
	{
		k_timer_stop(&encoder_debug_timer);
	}
	return 0;
}

SHELL_SUBCMD_DICT_SET_CREATE(encoder_print_cmds, cmd_encoder_print,
							 (enable, true, "enable"), (disable, false, "disable"));

static int cmd_pressure_control_calibrate_zero_pressure(const struct shell *sh, size_t argc, char **argv)
{
	ARG_UNUSED(argc);
	ARG_UNUSED(argv);
	return calibrate_zero_pressure();
}

static int cmd_test_pump(const struct shell *sh, size_t argc, char **argv)
{
	ARG_UNUSED(argc);
	ARG_UNUSED(argv);
	if (argc != 4)
	{
		goto print_pump_usage;
	}
	const struct device *pump;
	char *pump_name_capping = "capping";
	char *pump_name_ink = "ink";
	char *pump_name;
	if (strcmp(argv[1], "ink") == 0)
	{
		pump = DEVICE_DT_GET(DT_NODELABEL(ink_pump));
		pump_name = pump_name_ink;
	}
	else if (strcmp(argv[1], "capping") == 0)
	{
		pump = DEVICE_DT_GET(DT_NODELABEL(capping_pump));
		pump_name = pump_name_capping;
	}
	else
	{
		goto print_pump_usage;
	}
	motor_action_t action;
	if (strcmp(argv[2], "cw") == 0)
	{
		action = MOTOR_ACTION_CW;
	}
	else if (strcmp(argv[2], "ccw") == 0)
	{
		action = MOTOR_ACTION_CCW;
	}
	else if (strcmp(argv[2], "brake") == 0)
	{
		action = MOTOR_ACTION_SHORT_BRAKE;
	}
	else if (strcmp(argv[2], "stop") == 0)
	{
		action = MOTOR_ACTION_STOP;
	}
	else
	{
		goto print_pump_usage;
	}
	float speed = atof(argv[3]);
	if (!device_is_ready(pump))
	{
		LOG_ERR("Pump not ready");
		return -ENODEV;
	}
	shell_print(sh, "Setting pump %s to %d at %f", pump_name, action, (double)speed);
	motor_set_action(pump, action, speed);
	return 0;
print_pump_usage:
	shell_print(sh, "Usage: test_pump <ink|capping> <cw|ccw|brake|stop> <pwm>");
	return -EINVAL;
}

static int cmd_system_state(const struct shell *sh, size_t argc, char **argv, void *data)
{
	switch ((int)data)
	{
	case 0:
		k_timer_stop(&print_fire_timer);
		go_to_idle();
		break;
	case 1:
		go_to_dropwatcher();
		break;
	case 2:
		go_to_keep_alive();
	default:
		break;
	}
	return 0;
}

SHELL_SUBCMD_DICT_SET_CREATE(system_state_cmds, cmd_system_state,
							 (idle, 0, "idle"), (dropwatcher, 1, "dropwatcher"), (keepalive, 2, "keepalive"));

static int cmd_fire(const struct shell *sh, size_t argc, char **argv)
{
	if (argc != 3)
	{
		shell_print(sh, "Usage: fire <ms> <drop_count>");
		return EINVAL;
	}
	fire_count = 0;
	drop_count = atoi(argv[2]);
	int interval_us = atoi(argv[1]);
	const struct device *printhead = DEVICE_DT_GET(DT_NODELABEL(printhead));
	// uint32_t pixels[4] = {0xFFFFFFFF, 0xFFFFFFFF, 0xFFFFFFFF, 0xFFFFFFFF};
	// printer_set_pixels(printhead, pixels);
	k_timer_start(&print_fire_timer, K_USEC(interval_us), K_USEC(interval_us));
	return 0;
}

static void cmd_test_fire(const struct shell *sh, size_t argc, char **argv)
{
	ARG_UNUSED(argc);
	ARG_UNUSED(argv);
	const struct device *dev = DEVICE_DT_GET(DT_NODELABEL(printer_fire));
	if (gpio_pin_get_dt(&comm_enable) != 0)
	{
		shell_print(sh, "COMM_ENABLE must be low");
		return;
	}
	printer_fire_request_fire(dev);
}

static void cmd_enable_printhead_clock(const struct shell *sh, size_t argc, char **argv)
{
	ARG_UNUSED(argc);
	ARG_UNUSED(argv);
	const struct device *printhead = DEVICE_DT_GET(DT_NODELABEL(printhead));
	printer_clock_enable(printhead, PWM_HZ(1000000));
}

static int cmd_print_control_set_mode(const struct shell *sh, size_t argc, char **argv, void *data)
{
	ARG_UNUSED(argc);
	ARG_UNUSED(argv);
	uint32_t mode = (uint32_t)data;
	if (mode == 1)
	{
		print_control_start_manual_fire_mode();
	}
	else if (mode == 2)
	{
		print_control_encoder_mode_settings_t init = {
			.sequential_fires = 1,
			.fire_every_ticks = 1,
			.lines_to_print = 1000,
			.print_first_line_after_encoder_tick = 250};
		print_control_start_encoder_mode(&init);
	}
	else
	{
		shell_print(sh, "Invalid mode");
	}
	return 0;
}

static int cmd_regulator_get_voltage(const struct shell *sh, size_t argc, char **argv)
{
	ARG_UNUSED(argc);
	ARG_UNUSED(argv);
	uint32_t voltage;
	bool read = regulator_get_voltage(&voltage);
	if (!read)
	{
		shell_print(sh, "Failed to read voltage");
		return -EIO;
	}
	else
	{
		shell_print(sh, "Voltage: %d", voltage);
	}
	return 0;
}

static int cmd_regulator_set_voltage(const struct shell *sh, size_t argc, char **argv)
{
	if (argc != 2)
	{
		shell_print(sh, "Usage: regulator_set_voltage <voltage in mv>");
		return EINVAL;
	}
	double voltage = atof(argv[1]);
	int ret = regulator_set_voltage(voltage);
	if (ret != 0)
	{
		shell_print(sh, "Failed to set voltage");
	}
	return ret;
}

SHELL_SUBCMD_DICT_SET_CREATE(print_control_set_mode_cmds, cmd_print_control_set_mode,
							 (manual, 1, "manual"), (encoder, 2, "encoder"));

SHELL_STATIC_SUBCMD_SET_CREATE(sub_test,
							   SHELL_CMD(hv_supply, NULL, "Test HV supply", cmd_test_hv_supply),
							   SHELL_CMD(printhead_io, NULL, "Test printhead IO", cmd_test_printhead_io),
							   SHELL_CMD(other_io, NULL, "Test other IO", cmd_test_other_io),
							   SHELL_CMD(set_pixels, NULL, "Set pixels", cmd_set_pixels),
							   SHELL_CMD(comm_enable, NULL, "Set COMM_ENABLE", cmd_comm_enable),
							   SHELL_CMD(pressure_control_enable, &pressure_control_enable_cmds, "Enable/disable pressure control", NULL),
							   SHELL_CMD(pressure_control_print_pressure, &pressure_control_print_pressure_cmds, "Print pressure", NULL),
							   SHELL_CMD(encoder_print, &encoder_print_cmds, "Print encoder", NULL),
							   SHELL_CMD(print_control_set_mode, &print_control_set_mode_cmds, "Set print control mode", NULL),
							   SHELL_CMD(pressure_control_calibrate_zero_pressure, NULL, "Calibrate zero pressure", cmd_pressure_control_calibrate_zero_pressure),
							   SHELL_CMD(pump, NULL, "Test pump", cmd_test_pump),
							   SHELL_CMD(system_state, &system_state_cmds, "Set system state", cmd_system_state),
							   SHELL_CMD(fire, NULL, "Fire printhead", cmd_fire),
							   SHELL_CMD(test_fire, NULL, "Test fire", cmd_test_fire),
							   SHELL_CMD(enable_printhead_clock, NULL, "Enable printhead clock", cmd_enable_printhead_clock),
							   SHELL_CMD(regulator_get_voltage, NULL, "Get regulator voltage", cmd_regulator_get_voltage),
							   SHELL_CMD(regulator_set_voltage, NULL, "Set regulator voltage", cmd_regulator_set_voltage),
							   SHELL_SUBCMD_SET_END);
SHELL_CMD_REGISTER(test, &sub_test, "Test commands", NULL);

static void pressure_control_error()
{
	failure_handling_set_error_state(ERROR_PRESSURE_CONTROL);
}

static void failure_callback()
{
	printhead_routines_go_to_safe_state();
	pressure_control_go_to_safe_state();
	printer_system_smf_go_to_safe_state();
	print_control_go_to_safe_state();
}

static void printhead_routines_error()
{
	failure_handling_set_error_state(ERROR_PRINTHEAD_RESET);
}

static void printhead_control_error(uint32_t errors)
{
	failure_handling_set_error_state(errors);
}

int main(void)
{
	int ret;
	ret = initialize_io();
	if (ret != 0)
	{
		return ret;
	}

	if (!gpio_is_ready_dt(&button))
	{
		printk("Error: button device %s is not ready\n",
			   button.port->name);
		return 0;
	}

	ret = gpio_pin_configure_dt(&button, GPIO_INPUT);
	if (ret != 0)
	{
		printk("Error %d: failed to configure %s pin %d\n",
			   ret, button.port->name, button.pin);
		return 0;
	}

	ret = gpio_pin_interrupt_configure_dt(&button,
										  GPIO_INT_EDGE_TO_ACTIVE);
	if (ret != 0)
	{
		printk("Error %d: failed to configure interrupt on %s pin %d\n",
			   ret, button.port->name, button.pin);
		return 0;
	}

	gpio_init_callback(&button_cb_data, button_pressed, BIT(button.pin));
	gpio_add_callback(button.port, &button_cb_data);
	printk("Set up button at %s pin %d\n", button.port->name, button.pin);

	printk("Zephyr Example Application %s\n", APP_VERSION_STRING);
	const struct device *printhead;

	printhead = DEVICE_DT_GET(DT_NODELABEL(printhead));

	if (!device_is_ready(printhead))
	{
		LOG_ERR("Printhead not ready");
		return 0;
	}

	pressure_control_init_t pressure_control_init = {
		.error_callback = pressure_control_error};
	ret = pressure_control_initialize(&pressure_control_init);
	if (ret != 0)
	{
		LOG_ERR("Pressure control initialization failed with error %d", ret);
		return ret;
	}

	printhead_routines_init_t printhead_routines_init = {
		.error_callback = printhead_routines_error};
	ret = printhead_routines_initialize(&printhead_routines_init);
	if (ret != 0)
	{
		LOG_ERR("Printhead routines initialization failed with error %d", ret);
		return ret;
	}

	ret = regulator_initialize();
	if (ret != 0)
	{
		LOG_ERR("Regulator initialization failed with error %d", ret);
		return ret;
	}

	failure_handling_init_t failure_handling_init = {
		.failure_callback = failure_callback};
	ret = failure_handling_initialize(&failure_handling_init);
	if (ret != 0)
	{
		LOG_ERR("Failure handling initialization failed with error %d", ret);
		return ret;
	}

	print_control_init_t print_control_init = {
		.error_callback = printhead_control_error};
	ret = print_control_initialize(&print_control_init);
	if (ret != 0)
	{
		LOG_ERR("Print control initialization failed with error %d", ret);
		return ret;
	}
	
	ret = printer_system_smf();
	if (ret != 0)
	{
		LOG_ERR("Printer system state machine terminated with error %d", ret);
		return ret;
	}
	return 0;
}

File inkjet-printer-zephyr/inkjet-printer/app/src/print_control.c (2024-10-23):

#include <zephyr/device.h>
#include <zephyr/logging/log.h>
#include <zephyr/drivers/sensor.h>

#include <lib/inkjetcontrol/encoder.h>
#include <lib/inkjetcontrol/nozzle_data.h>
#include <lib/inkjetcontrol/test_pattern.h>
#include <zephyr/drivers/printer.h>
#include <zephyr/drivers/printer_fire.h>

#include "print_control.h"
#include "failure_handling.h"

LOG_MODULE_REGISTER(print_control, CONFIG_APP_LOG_LEVEL);

static uint32_t print_memory[16384] = {0};

static const struct device *printhead;
static const struct device *printer_fire;
static const struct device *encoder;

static print_control_error_callback_t error_callback;

static encoder_print_status_t encoder_print_status;

static uint32_t line_to_load = 0;
static bool next_load_wait_fired = false;

static void load_line_handler(void);

K_SEM_DEFINE(load_line_sem, 0, 1);

static encoder_mode_t encoder_mode = ENCODER_MODE_OFF;

static bool nozzle_priming_active = false;

static void load_line_handler(void)
{
    while (true)
    {
        k_sem_take(&load_line_sem, K_FOREVER);
        int ret;
        if (next_load_wait_fired)
        {
            ret = printer_wait_fired_load_next(printhead, K_USEC(20));
            LOG_INF("Wait fired %d", ret);
            if (ret != 0)
            {
                LOG_ERR("Fired signal not received, skipping load");
                continue;
            }
        }
        ret = printer_set_pixels(printhead, &print_memory[line_to_load * 4]);
        if (ret != 0)
        {
            error_callback(ERROR_PRINTHEAD_COMMUNICATION);
        }
        encoder_signal_load_line_completed(&encoder_print_status, line_to_load);
    }
}

static int32_t get_value_cb(void *inst)
{
    struct sensor_value val;
    (void)sensor_sample_fetch(encoder);
    (void)sensor_channel_get(encoder, SENSOR_CHAN_POS_DX, &val);
    return val.val1;
}

static void load_error_cb(void *inst)
{
    LOG_ERR("Load error");
}

static void fire_abort_cb(void *inst)
{
    printer_fire_abort(printer_fire);
}

static void load_line_cb(void *inst, uint32_t line, bool wait_fired)
{
    line_to_load = line;
    next_load_wait_fired = wait_fired;
    k_sem_give(&load_line_sem);
}

static void fire_issued_cb()
{
    if (encoder_mode == ENCODER_MODE_ON)
    {
        encoder_fire_issued_handler(&encoder_print_status);
    }
}

static void fire_completed_cb()
{
    if (encoder_mode == ENCODER_MODE_ON)
    {
        encoder_fire_cycle_completed_handler(&encoder_print_status);
    }
}

static void trigger_cb()
{
    if (encoder_mode == ENCODER_MODE_ON)
    {
        encoder_tick_handler(&encoder_print_status);
    }
}

int print_control_start_encoder_mode(print_control_encoder_mode_settings_t *init)
{
    static encoder_print_init_t print_init = {
        .fire_abort = fire_abort_cb,
        .get_value = get_value_cb,
        .load_line = load_line_cb,
        .load_error_cb = load_error_cb,
        .inst = NULL};
    print_init.sequential_fires = init->sequential_fires;
    print_init.fire_every_ticks = init->fire_every_ticks;
    print_init.print_first_line_after_encoder_tick = init->print_first_line_after_encoder_tick;
    print_init.lines_to_print = init->lines_to_print;
    encoder_print_init(&encoder_print_status, &print_init);
    printer_fire_set_timing(printer_fire, 10300, 1000, 10300, 2000);
    printer_fire_set_fire_issued_callback(printer_fire, fire_issued_cb);
    printer_fire_set_fire_cycle_completed_callback(printer_fire, fire_completed_cb);
    printer_fire_set_trigger_callback(printer_fire, trigger_cb);
    printer_fire_set_trigger_reset(printer_fire, true);
    printer_fire_abort(printer_fire);
    printer_fire_set_trigger(printer_fire, PRINTER_FIRE_TRIGGER_CLOCK);
    if (init->start_paused)
    {
        encoder_mode = ENCODER_MODE_PAUSED;
    }
    else
    {
        printer_fire_set_trigger(printer_fire, PRINTER_FIRE_TRIGGER_ENCODER);
        printer_fire_set_trigger_reset(printer_fire, false);
        printer_fire_request_fire(printer_fire);
        encoder_mode = ENCODER_MODE_ON;
    }
    return 0;
}
int print_control_start_manual_fire_mode()
{
    encoder_mode = ENCODER_MODE_OFF;
    printer_fire_set_timing(printer_fire, 40000, 1000, 250, 1000);
    printer_fire_set_trigger(printer_fire, PRINTER_FIRE_TRIGGER_CLOCK);
    printer_fire_set_trigger_reset(printer_fire, true);
    printer_fire_set_fire_issued_callback(printer_fire, NULL);
    printer_fire_set_fire_cycle_completed_callback(printer_fire, NULL);
    printer_fire_set_trigger_callback(printer_fire, NULL);
    return 0;
}
int print_control_request_fire()
{
    int ret = printer_fire_request_fire(printer_fire);
    if (ret != 0)
    {
        error_callback(ERROR_PRINTHEAD_FIRE);
        return ret;
    }
    return 0;
}

void print_control_set_encoder_position(int32_t value)
{
    struct sensor_value val;
    (void)sensor_sample_fetch(encoder);
    (void)sensor_channel_get(encoder, SENSOR_CHAN_POS_DX, &val);
    val.val1 = value - val.val2;
    (void)sensor_attr_set(encoder, SENSOR_CHAN_POS_DX, SENSOR_ATTR_OFFSET, &val);
}

void print_control_disable()
{
    encoder_mode = ENCODER_MODE_OFF;
    printer_fire_set_trigger_reset(printer_fire, true);
    printer_fire_abort(printer_fire);
    printer_fire_set_trigger(printer_fire, PRINTER_FIRE_TRIGGER_CLOCK);
}

void print_control_set_print_memory(uint32_t offset, uint32_t *data, uint32_t length)
{
    memcpy(&print_memory[offset], data, length * sizeof(uint32_t));
}

int print_control_initialize(print_control_init_t *init)
{
    error_callback = init->error_callback;
    printhead = DEVICE_DT_GET(DT_NODELABEL(printhead));
    if (!device_is_ready(printhead))
    {
        LOG_ERR("Printhead not ready");
        return -ENODEV;
    }
    printer_fire = DEVICE_DT_GET(DT_NODELABEL(printer_fire));
    if (!device_is_ready(printer_fire))
    {
        LOG_ERR("Printer fire not ready");
        return -ENODEV;
    }
    encoder = DEVICE_DT_GET(DT_NODELABEL(qdec));
    if (!device_is_ready(encoder))
    {
        LOG_ERR("Encoder device is not ready");
        return -ENODEV;
    }
    return 0;
}

void print_control_go_to_safe_state()
{
    printer_fire_set_trigger_reset(printer_fire, true);
    printer_fire_abort(printer_fire);
    printer_fire_set_trigger(printer_fire, PRINTER_FIRE_TRIGGER_CLOCK);
}
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

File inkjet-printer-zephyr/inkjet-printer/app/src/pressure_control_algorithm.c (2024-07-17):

#include <zephyr/logging/log.h>
#include "pressure_control_algorithm.h"
#include "moving_average.h"

#define MIN_PRESSURE_CHANGE_PER_SECOND_AT_FULL_SPEED (0.1f)
#define MAX_TIME_LOW_PRESSURE_CHANGE_SECONDS (5.0f)
#define LOW_PRESSURE_CHANGE_CONDITION_EXIT_SECONDS (0.5f)

static const float k_p = 0.15;
static const float k_i = 0.5;
static const float max_i = 1.0;
static const float min_pwm = 0.3;

typedef struct
{
    pressure_control_algorithm_motor_result_t motor_result;
    bool done;
    bool failure_detected;
} pressure_control_algorithm_result_t;

typedef struct
{
    float i;
    float last_error_abs;
    float last_pwm;
    float time_with_low_pressure_change;
    float time_without_low_pressure_change;
    bool low_pressure_condition;
    moving_average_t error_moving_average;
} target_pressure_state_t;

typedef struct 
{
    float feed_time;
} feed_with_limit_state_t;

static target_pressure_state_t target_pressure_state[NUM_PUMPS];
static feed_with_limit_state_t feed_with_limit_state[NUM_PUMPS];


LOG_MODULE_REGISTER(pressure_control_alg, CONFIG_APP_LOG_LEVEL);

static void pressure_control_algorithm_target_pressure(
    uint32_t pump_idx,
    const pressure_control_algorithm_params_t *params,
    pressure_control_algorithm_result_t *result)
{
    target_pressure_state_t *state = &target_pressure_state[pump_idx];
    if (params->initial_run)
    {
        state->i = 0;
        state->time_with_low_pressure_change = 0;
        state->time_without_low_pressure_change = 0;
        state->low_pressure_condition = false;
        moving_average_init(&state->error_moving_average);
    }
    float error = params->algorithm[pump_idx].target_pressure - params->current_pressure;
    float error_abs = error > 0 ? error : -error;

    if (error_abs < 0.5f)
    {
        result->done = true;
        error = 0;
        error_abs = 0;
    }
    state->i += error * params->elapsed_time_seconds;
    if (state->i > max_i)
    {
        state->i = max_i;
    }
    if (state->i < -max_i)
    {
        state->i = -max_i;
    }
    float pwm = k_p * error + k_i * state->i;

    float pwm_abs = pwm > 0 ? pwm : -pwm;
    if (pwm_abs > 1)
    {
        pwm_abs = 1;
    }

    if (pwm_abs > min_pwm)
    {
        result->motor_result.action = pwm > 0 ? MOTOR_ACTION_CCW : MOTOR_ACTION_CW;
        result->motor_result.pwm = pwm_abs;
    }
    else
    {
        result->motor_result.action = MOTOR_ACTION_STOP;
    }

    if (!params->initial_run && result->motor_result.action != MOTOR_ACTION_STOP)
    {
        // Note, that the moving average size must fit to the control loop frequency, because short term the pressure does not change much if there
        // is a big volume
        moving_average_add(&state->error_moving_average, error_abs - state->last_error_abs);
        LOG_INF("Sum %f, %f, %f", state->error_moving_average.sum, state->error_moving_average.avg, error_abs);
        if (state->error_moving_average.avg >= 0 && !state->low_pressure_condition)
        {
            state->low_pressure_condition = true;
            state->time_with_low_pressure_change = 0;
            state->time_without_low_pressure_change = 0;
        }
        if (state->low_pressure_condition)
        {
            LOG_INF("Low pressure condition, %f, %f, %f", state->time_with_low_pressure_change, state->time_without_low_pressure_change, state->error_moving_average.avg);
            if (state->error_moving_average.avg < 0)
            {
                state->time_without_low_pressure_change += params->elapsed_time_seconds;
                if (state->time_without_low_pressure_change > LOW_PRESSURE_CHANGE_CONDITION_EXIT_SECONDS)
                {
                    state->low_pressure_condition = false;
                }
            }
            else
            {
                state->time_without_low_pressure_change = 0;
                state->time_with_low_pressure_change += params->elapsed_time_seconds;
                if (state->time_with_low_pressure_change > MAX_TIME_LOW_PRESSURE_CHANGE_SECONDS)
                {
                    result->failure_detected = true;
                }
            }
        }
    }
    else
    {
        state->low_pressure_condition = true;
        state->time_with_low_pressure_change = 0;
        state->time_without_low_pressure_change = 0;
    }
    state->last_error_abs = error_abs;
    state->last_pwm = result->motor_result.pwm;
}
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

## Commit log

2023-11-17 circuit working with led
2023-12-11 fpc adapter & strobe
    [FPC_Adapter.kicad_pcb, FPC_Adapter.kicad_sch, Strobe.kicad_pcb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]
2023-12-11 Xaar Driver & Adapter
    [Xaar128-Adapter.kicad_pcb, Xaar128-Adapter.kicad_sch, Xaar128-Driver.kicad_pcb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]
2023-12-11 adapter mostly done
    [Xaar128-Adapter.kicad_pcb, Xaar128-Adapter.kicad_sch]
2023-12-12 finish Xaar128-Adapter
    [Xaar128-Adapter.kicad_pcb]
2023-12-12 5v monitoring
    [Xaar128-Driver.kicad_pcb, Xaar128-Driver.kicad_sch, hv_supply.kicad_sch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]
2023-12-12 some component selections, fix wrong mcu
    [hv_supply.kicad_sch, io.kicad_sch, level_shift.kicad_sch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]
2023-12-13 assign footprints
    [hv_supply.kicad_sch, io.kicad_sch, level_shift.kicad_sch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]
2023-12-15 select remaining components, nucleo footprint
    [Xaar128-Driver.kicad_pcb, hv_supply.kicad_sch, level_shift.kicad_sch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]
2023-12-18 start xaar driver routing
    [Xaar128-Driver.kicad_pcb, level_shift.kicad_sch]
2023-12-18 xaar driver: some routed islands
    [FPC_Adapter.kicad_pcb, FPC_Adapter.kicad_sch, Strobe.kicad_pcb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]
2023-12-18 xaar driver pcb: order elements
    [Xaar128-Driver.kicad_pcb]
2023-12-22 more components routed
    [Xaar128-Driver.kicad_pcb, mcu.kicad_sch]
2023-12-28 more routing
    [Xaar128-Driver.kicad_pcb, level_shift.kicad_sch, mcu.kicad_sch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]
2024-01-04 routing done
    [Xaar128-Driver.kicad_pcb, level_shift.kicad_sch, regulator.kicad_sch]
2024-01-05 drc & plots done
    [Xaar128-Adapter.kicad_pcb, Xaar128-Driver.kicad_pcb, hv_supply.kicad_sch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]
2024-01-08 add acc and text
    [Xaar128-Driver.kicad_pcb, Xaar128-Driver.kicad_sch, acc.kicad_sch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]
2024-01-08 fix caps
    [hv_supply.kicad_sch]
2024-01-08 create order list
    [Xaar128-Adapter.csv, Xaar128-Adapter.kicad_pcb, Xaar128-Adapter.kicad_sch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]
2024-01-08 Create plots for fabrication
    [Xaar128-Adapter.kicad_pcb, Xaar128-Driver.kicad_pcb]
2024-01-11 received parts
    [ordered.csv]
2024-01-12 bootstrap Xaar-128-Driver-Firmware
    [st_nucleo_h7a3ziq.cfg]
2024-01-15 received last item
    [ordered.csv]
2024-01-17 switch mcu
    [Xaar128-Driver.kicad_sch, acc.kicad_sch, hv_supply.kicad_sch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]
2024-01-17 strobe/nfire timer combined pwm mode
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2024-01-24 combined pwm fire working
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2024-02-23 driver for motor and pressure sensor
2024-02-23 pump and pressure sensor perfboard
    [pressure-sensor.kicad_pcb, pressure-sensor.kicad_sch, pump.kicad_pcb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]
2024-02-23 implement pressure control on nucleo
    [pump.kicad_pcb, pump.kicad_sch]
2024-02-28 fire cmd + spi fixed
    [main.c, printer_system_smf.c, xaar128.c]
2024-03-08 downgrade zephyr to fix webusb
    [printer_system_smf.c, stm32_combined_pwm.c, webusb.c]
2024-03-11 fix light and fire timing
    [stm32_combined_pwm.c, webusb.c]
2024-03-13 fix pressure control timout, refactor it, webusb system state
    [main.c, pressure_control.c]
2024-03-22 pressure control using webapp
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2024-03-27 handle printhead ready, nozzle data via usb
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2024-04-13 inventor cad models
    [CameraHolder.ipt, Capping_Assembly.iam, Capping_Cover.ipt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]
2024-04-18 cad sync
    [Capping_Parallelizer.ipt, Dreiwegehahn_Halter.ipt, Pressuresensor_Holder.ipt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]
2024-04-19 fix nozzle bit/shift order
    [printer_system_smf.c, xaar128.c]
2024-04-19 higher camera holder
    [CameraHolderV2.ipt]
2024-04-29 encoder mount1
    [Encoder1.iam, Encoder_Mount1.iam, Encoder_Mount1_Slider.ipt]
2024-05-06 capping assembly 2 start
    [Capping_Assembly2.iam, Capping_Insert.ipt, Capping_RotationAnchor.ipt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]
2024-05-06 rotating capping first print
    [Capping_Assembly2.iam, Capping_Insert.ipt, Capping_RotatingArm.ipt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]
2024-05-06 encoder mount
    [Beltspanner.ipt, Encoder_Cable_Clamp.ipt, Encoder_Mount1.iam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]
2024-05-08 rotating capping
    [Capping_Assembly2.iam, Capping_RotatingArm.ipt, Capping_RotatingCover.ipt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]
2024-05-16 capping two magnets
    [Capping_Assembly2.iam, Capping_RotatingArm.ipt, Capping_RotationAnchor.ipt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]
2024-05-17 asa cover
    [Capping_RotatingCover.ipt]
2024-05-19 fix references
    [Capping_Assembly2.iam, Capping_RotatingArm.ipt]
2024-05-21 capping rubber printed
    [Capping_Assembly2.iam, Capping_RotationAnchor.ipt, Capping_RubberInsert.ipt]
2024-05-21 capping straight
    [Capping_Assembly2.iam, Capping_RotatingArm.ipt, Capping_RotationAnchor.ipt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]
2024-05-24 ordering voltage regulator extension
    [Xaar128-Adapter.csv, Xaar128-Adapter.kicad_sch, Xaar128-Driver.csv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]
2024-05-28 prepare encoder library for testing
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2024-05-29 encoder diagrams
    [Encoder_Skipping.xlsx]
2024-05-29 cad stuff
    [Capping_Assembly2.iam, Capping_RotatingArm.ipt, Encoder_Mount3_Base.ipt]
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2024-05-29 fix direct timer references
    [qdec_stm32_linear.c, stm32_combined_pwm.c]
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2024-06-10 print memory, flip encoder direction
    [print_control.c, qdec_stm32_linear.c, webusb.c]
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2024-06-26 remove cubemx project
    [st_nucleo_h7a3ziq.cfg]
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2024-07-02 slicer moved to worker, fix start print in the middle bug
    [main.c, print_control.c, stm32_combined_pwm.c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]
2024-07-05 nozzle correction kind of working
2024-07-07 perfboard supports two pumps
    [pump.kicad_pcb, pump.kicad_sch]
2024-07-07 add cable slot to pump mount
    [Pump_Mount.ipt]
2024-07-08 microscope mount
    [Microscope_Mount.ipt]
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2024-07-08 perfboard with second pump
    [pump.kicad_pcb, pump.kicad_sch]
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2024-07-15 fix dac address r
    [Xaar128-Driver.kicad_pcb, Xaar128-Driver.kicad_sch, acc.kicad_sch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]
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2024-07-17 heatbed pcb
    [Heatbed.kicad_pcb, Heatbed.kicad_sch]
2024-07-19 final heatbed circuit
    [Heatbed.kicad_pcb, Heatbed.kicad_sch]
2024-07-22 switch opv to lm358
    [Xaar128-Driver.kicad_pcb, regulator.kicad_sch]
2024-07-26 camera calibration & layers calculation
    [camera_calibration.xlsx]
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2024-08-09 prevent move down when homing
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2024-08-25 correct pmos
    [hv_supply.kicad_sch, regulator.kicad_sch]
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2024-08-29 fix randomize bug, semi automatic nozzle test working
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2024-09-02 camera: timeout; task runner: resume failed
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2024-11-18 fix nmos
    [reset_circuit.kicad_sch]
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2025-02-26 fix visual homing
2025-03-02 remove legacy cad files
    [CameraHolder.ipt, Capping_Assembly.iam, Capping_Cover.ipt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]
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2025-03-02 remove legacy strobe pcb
    [Strobe.kicad_pcb, Strobe.kicad_sch]
2025-03-02 remove unrelated docs and tools
    [Encoder_Skipping.xlsx, camera_calibration.xlsx]
2025-03-02 remove fpc-adapter
    [FPC_Adapter.kicad_pcb, FPC_Adapter.kicad_sch]
2025-03-02 move pcbs to pcbs folder
    [Heatbed.kicad_pcb, Heatbed.kicad_sch, Xaar128-Adapter.csv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]
